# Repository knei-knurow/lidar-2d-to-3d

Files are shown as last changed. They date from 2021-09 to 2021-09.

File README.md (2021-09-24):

# Lidar 2D to 3D

Celem projektu było stworzenie urządzenia zdolnego do skanowania otaczającej go
przestrzeni w 3D z użyciem lidaru 2D.

ezgif-3-d5575b524c23

# Spis treści

- [Galeria](#galeria)
  - [3D](#3d)
  - [2D](#2d)
- [Submoduły](#submoduły)
  - [lidar-tools\*](#lidar-tools)
    - [sync\*](#sync)
    - [servoctl](#servoctl)
    - [receiver/transmitter](#transmitterreceiver)
    - [scan-dummy](#scan-dummy)
  - [lidar-avr\*](#lidar-avr)
  - [lidar-scan\*](#lidar-scan)
  - [lidar-vis](#lidar-vis)
  - [lidar-visualizations](#lidar-visualizations)
  - [lidar-stm32](#lidar-stm32)
- [Elementy](#elementy)
  - [Lidar](#lidar)
    - [Specyfikacja](#specyfikacja)
    - [Źródła](#źródła)
    - [Tryby skanowania](#tryby-skanowania)
    - [Dane](#dane)
    - [Pomiary szybkości silnika lidaru](#pomiary-szybkości-silnika-lidaru)
    - [Ogólne pomiary rezultatów lidaru](#ogólne-pomiary-rezultatów-lidaru)
  - [Serwomechanizm](#serwomechanizm)
  - [IMU](#imu)
    - [MPU-6050](#mpu-6050)
    - [MPU-9250](#mpu-9250)
    - [Kalibracja](#kalibracja)
    - [DMP](#dmp)
  - [Mikrokontroler](#mikrokontroler)
  - [Głowica](#głowica)
- [Skanowanie 3D](#skanowanie-3d)
  - [Obróbka surowych pomiarów IMU](#obróbka-surowych-danych-imu)
- [Konfiguracja](#konfiguracja)
  - [Hardware](#hardware)
  - [Software](#software)
    - [Parametry _lidar-tools/sync_](#parametry-lidar-toolssync)
- [Materiały](#materiały)
  - [Oprogramowanie pomocnicze](#oprogramowanie-pomocnicze)
  - [Przykłady chmur punktów](#przykłady-chmur-punktów)

# Galeria

## 3D

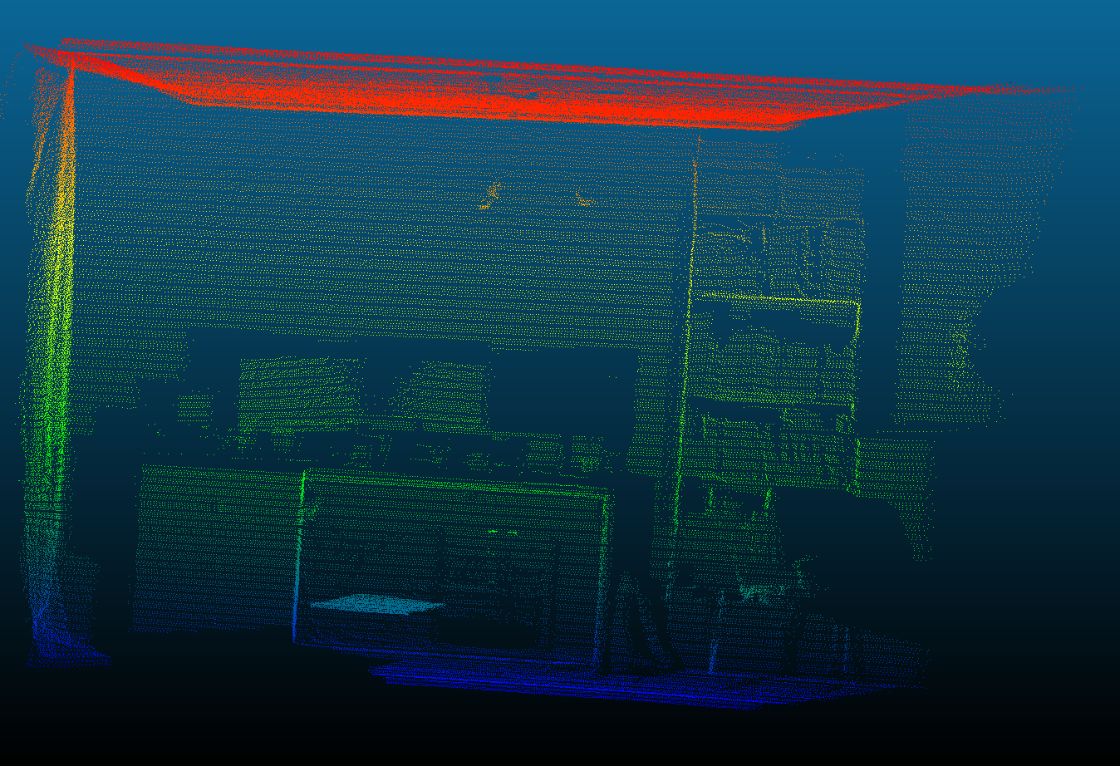
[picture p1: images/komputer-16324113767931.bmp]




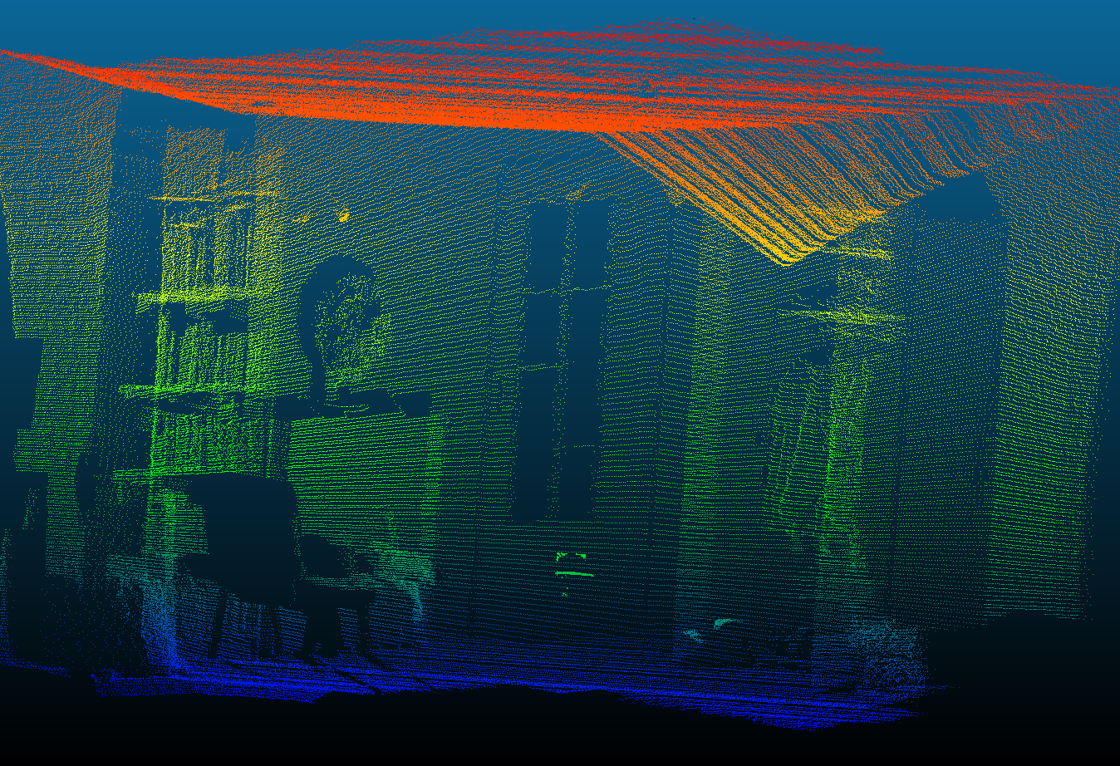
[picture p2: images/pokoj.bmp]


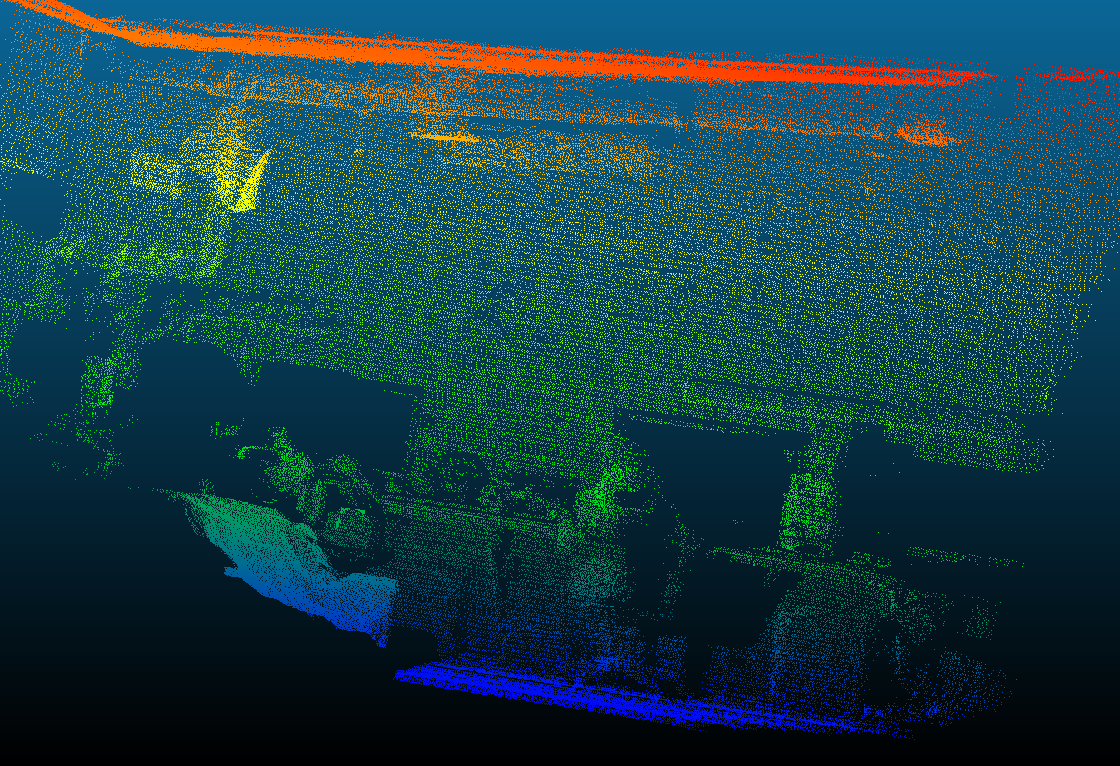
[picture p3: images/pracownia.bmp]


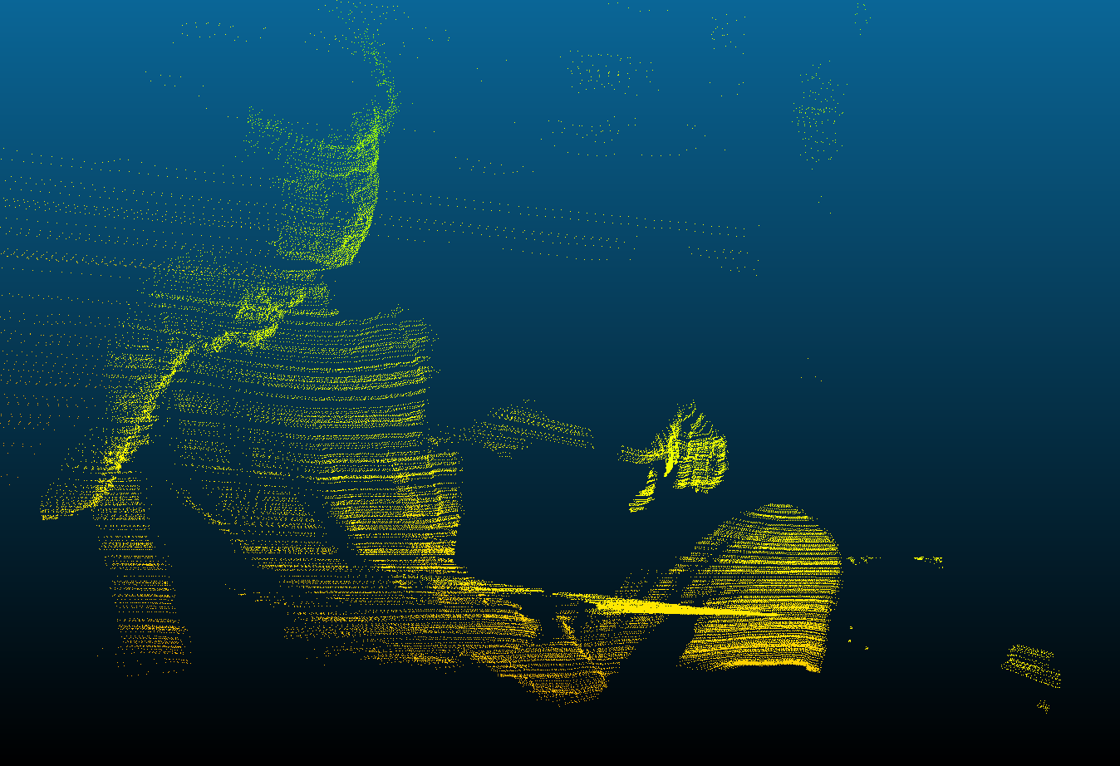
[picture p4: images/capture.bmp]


## 2D

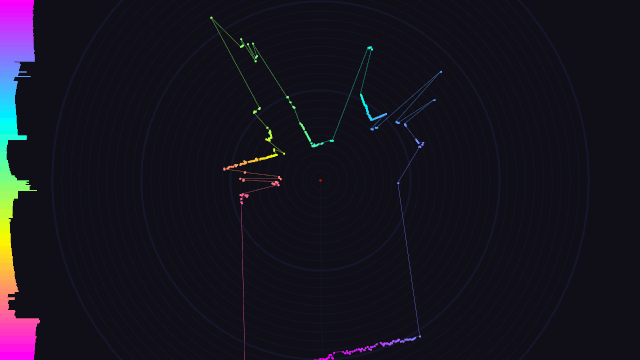
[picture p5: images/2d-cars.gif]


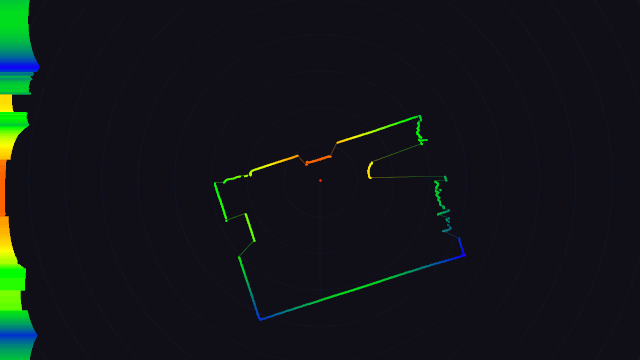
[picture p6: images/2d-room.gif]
2d-room


# Submoduły

W tym repozytorium pod jednym dachem zebrane są repozytoria z przedrostkiem
**lidar-** rozwijane w ramach [KNEI](https://github.com/knei-knurow), które
mają związek ze skanowaniem 3D. Więcej informacji o każdym
z tych projektów można znaleźć w ich plikach README.

**Gwiazdka \* oznacza repozytoria, które są wymagane do skanowania 3D.**
Pozostałe projekty mogą się przydać podczas zabawy ze skanowaniem 2D.

## lidar-tools\*

Zbiór programów _narzędzi_ przydatnych podczas pracy z lidarem.

### sync\*

Najważniejsze z _narzędzi_. Do jego zadań należy:

- Ustanowienie połączenia z mikrokontrolerem (który steruje serwem i
  akcelerometrem) oraz lidarem.
- Synchronizacja danych/pomiarów z dostępnych źródeł.
- Obliczanie punktów chmury 3D.
- Wypisywanie punkt po punkcie (x, y, z) na standardowe wyjście (stdout).

### servoctl

Wysyła do mikrokontrolera ramkę danych ustawiającą serwomechanizmu na zadanej pozycji.

### transmitter/receiver

Wysyła/odbiera dane lidaru 2D (uzyskane np. za pomocą _lidar-scan_) przez UDP.

### scan-dummy

Udaje _lidar-scan_. Generuje przykładowe dane.

**Autorzy:** [Szymon Bednorz](https://github.com/github.com/dsonyy),
[Bartek Pacia](https://github.com/github.com/bartekpacia)

## lidar-avr\*

Oprogramowanie przeznaczone do bycia wgranym na mikrokontroler AVR Atmega328p,
którego zadaniem jest obsługa serwomechanizmu i akcelerometru oraz komunikacja poprzez
USART z urządzeniem operatora.

Więcej o dokładnej konfiguracji i działaniu w dalszych sekcjach tego
dokumentu.

**Autorzy:** [Szymon Bednorz](https://github.com/github.com/dsonyy),
[Bartek Pacia](https://github.com/github.com/bartekpacia)

## lidar-scan\*

Projekt wywodzący się z _lidar-visualizations._ Pomysł polegał na stworzeniu
programu, który [robi jedną rzecz i robi ją dobrze](https://en.wikipedia.org/wiki/Unix_philosophy).

Zadaniem programu jest ustanowienie połączenia z lidarem oraz wypisywanie na
standardowe wyjście (stdout) odebranych danych w formie tekstowej. Docelowo
dane mogą być przekazane dowolnemu innemu programowi, który rozumie wejściowy
format danych.

Zgodny z systemami Linux, macOS, Windows.

**Przykładowe wyjście:**

```
# A comment
# ! ID Number   Elapsed time [ms]
# Angle [°]   Distance [mm]
! 0 0
120  100
240  100
360  100
! 1 500
120  200
240  200
360  200
! 2 500
```

**Autorzy:** [Szymon Bednorz](https://github.com/github.com/dsonyy),
[Bartek Pacia](https://github.com/github.com/bartekpacia)

## lidar-vis

Graficzie wyświetla dane otrzymane z lidaru za pomocą _lidar-scan_.

Projekt wywodzący się z _lidar-visualizations_. Jest to "siostrzany" program do
\_lidar-scan – [robi jedną rzecz i robi ją dobrze](https://en.wikipedia.org/wiki/Unix_philosophy).

Zgodny z systemami Linux, macOS, Windows.

**Autorzy:** [Szymon Bednorz](https://github.com/github.com/dsonyy),
[Bartek Pacia](https://github.com/bartekpacia)

## lidar-visualizations

Wyświetla dane z lidaru w postaci tekstowej lub graficznej w czasie rzeczywistym.

Oprogramowanie kilkukrotnie zmieniło prawie całkowicie swoją formę. Stworzone
zostało na potrzeby artykułu do "Elektroniki Praktycznej". Na chwilę obecną
nie jest aktywnie rozwijane. Kod składa się z kilku interfejsów, które
teoretycznie umożliwiają tworzenie dodatkowych funkcjonalności. Program
korzysta z oficjalnego RPLIDAR SDK oraz wysokopoziomowej biblioteki
graficznej SFML.

Zgodny z systemami Linux, macOS, Windows.

Więcej informacji można przeczytać w artykule ["Wizualizacja pomiarów skanera LIDAR"](https://ep.com.pl/kursy/notatnik-konstruktora/14763-wizualizacja-pomiarow-skanera-lidar) w ["Elektronice Praktycznej"](https://ep.com.pl) z marca 2021.

**Autor:** [Szymon Bednorz](https://github.com/github.com/dsonyy)

## lidar-stm32

Ciekawy projekt, który podobnie jak _lidar-visualizations_, stworzony został na
potrzeby "Elektroniki Praktycznej". Uruchamiany jest na płytce STM32, która za
pomocą UART wysyła/odbiera dane do/z lidaru, a następnie je wizualizuje.

RPLIDAR SDK nie jest przystosowany do urządzeń _embeddeed_, więc na jego
podstawie stworzona została autorska implementacja przeznaczona na STM32.

Więcej informacji można przeczytać w artykule ["Wizualizacja pomiarów skanera LIDAR"](https://ep.com.pl/kursy/notatnik-konstruktora/14763-wizualizacja-pomiarow-skanera-lidar) w ["Elektronice Praktycznej"](https://ep.com.pl) z marca 2021.

**Autor:** [Bartek Dudek](https://github.com/github.com/doodek)

# Elementy

## Lidar

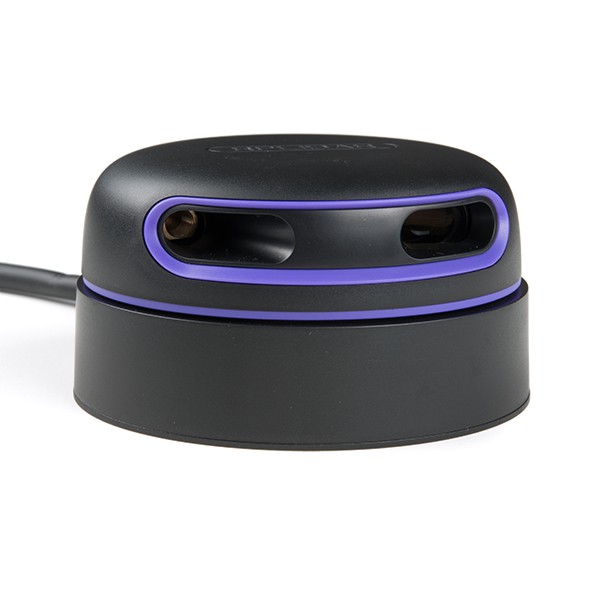
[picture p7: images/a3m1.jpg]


Wykorzystywany w projekcie lidar to [Slamtec RPLIDAR A3](https://www.slamtec.com/en/Lidar/A3Spec).
Producent dostarcza także [RPLIDAR SDK](https://github.com/Slamtec/rplidar_sdk)
wspierające systemy Linux, macOS i Windows, które pozwala na pracę ze sprzętem.

Lidar posiada swoje własne zasilanie. Dysponuje również przewodem USB, aby
przesyłać dane do urządzenia operatora.

### Specyfikacja

| Wielkość | A3 |
| --- | --- |
| Zakres pomiarów | do 25m |
| Częstotliwość pomiarów | do 16kHz |
| Częstotliwość wykonywania chmur | 5Hz - 20Hz |
| Rozdzielczość kątowa | do 0.225°  |
| Interfejs komunikacji | TTL UART |
| Prędkość komunikacji | 256000bps  |

### Źródła

- [RPLIDAR A3](https://www.slamtec.com/en/Lidar/A3)
- [SDK GitHub](https://github.com/Slamtec/rplidar_sdk)
- [RPLIDAR A3 User Manual](https://download.kamami.pl/p573426-LM310_SLAMTEC_rplidarkit_usermanual_A3M1_v1.0_en.pdf)
- [RPLIDAR A3 Introduction and Datasheet](https://download.kamami.pl/p573426-LD310_SLAMTEC_rplidar_datasheet_A3M1_v1.3_en.pdf)

### Tryby skanowania

RPLIDAR oferuje kilka trybów skanowania. Godne uwagi są tylko dwa: domyślny
sensitivity (indoor) i stability (outdoor). Podczas pracy na zewnątrz,
szczególnie w bardzo słoneczne dni, wyraźnie widać różnicę w ilości poprawnie
wykonanych pomiarów. Pozostałe tryby istnieją dla kompatybilności wstecznej z poprzednimi generacjami urządzenia i/lub wymagają niższego baudrate'u podczas transmisji danych.

| ID  | Scan mode | Sample time [us] | Frequency |
| --- | --- | --- | --- |
| 0 | Standard | 252 | 0.484406  |
| 1 | Express | 126 | 0.968812  |
| 2 | Boost | 63 | 1.93762 |
| 3 | **Sensitivity/Indoor (domyślny)** | 63 | 1.93762 |
| 4 | **Stability/Outdoor** | 100 | 1.2207 |

### Dane

- Domyślnym formatem danych lidaru są pary (kąt, odległość) w jednostkach
  [stopnie, milimetry].
- Pary pomiarów są pogrupowane po 360 stopni - jedna chmura punktów.
- Jeżeli pomiar dla danego kąta się nie powiódł, wartość odległości jest równa 0.
- Maksymalna ilość punktów w jednej chmurze to 8192, jest to narzucone przez
  producenta ograniczenie.
- Ilość punktów w chmurze - 360 stopniach - zależy od trybu skanowania oraz od
  ilości obrotów na minutę (ang. RPM, revolutions per minute). Im wolniejsza prędkość obrotu, tym więcej punktów w chmurze. Zalecany przez autora zakres pracy to od 200 do 1023 rpm. Przy mniejszych wartościach niż 200 istnieje ryzyko przekroczenia wartości 8192 punktów na chmurę co może powodować problemy. Domyśla wartość to 660rpm.

### Pomiary szybkości silnika lidaru

| Software RPM | Measured RPM | Software RPS | Measured RPS | Error  |
| --- | --- | --- | --- | --- |
| 200 | 196.62 | 3.33 | 3.28 | ~1.7%  |
| 400 | 432.02 | 6.67 | 7.20 | ~8.0%  |
| 600 | 684.52 | 10.00 | 11.41 | ~14.0% |
| 800 | 965.14 | 13.33 | 16.09 | ~20.6% |
| 1000 | 1268.98 | 16.67 | 21.15 | ~26.8% |

### Ogólne pomiary rezultatów lidaru

Tryb skanowania: **Sensitivity**

| zadany RPM | całk. czas [s] | punktów | punktów na chmurę | chmur | śr. czas na chmurę [s] | zmierzony RPM |
| --- | --- | --- | --- | ----- | --- | --- |
| 200 | 28.369 | 447133  | 4860.14 | 92 | 0.31 | 194.58 |
| 400 | 28.187 | 444097  | 2198.50 | 202 | 0.14 | 429.99 |
| 600 | 28.308 | 446794  | 1387.56 | 322 | 0.09 | 682.49 |
| **660\***  | 28.378 | 448529  | 1274.23 | 352 | 0.08 | 744.24 |
| 800 | 26.792 | 423121  | 984.00 | 430 | 0.06 | 962.97 |
| 1000 | 27.327 | 432130  | 748.93 | 577 | 0.05 | 1266.88 |

\* domyślny

## Serwomechanizm

Serwomechanizm odpowiada za obrót płaszczyzny, która jest skanowana przez lidar.
Sterowane jest ono sygnałem PWM za pomocą mikrokontrolera.

Wymaga własnego zasilania.

## IMU

IMU (ang. inertial measurement unit) to urządzenie służące do nawigacji
inercyjnej wyposażone w akcelerometr i żyroskop. Układ wykorzystywany przez nas
to **MPU-6050** o 6 stopniach swobody (akcelerometr X, Y, Z i żyroskop X, Y, Z).
W początkowej fazie rozwoju projektu zauważono, że konstrukcja składająca się z
samego lidaru i serwa może być podatna na niedokładności spowodowane tym, że:

- konstrukcja podczas ruchu mogłaby być mniej lub bardziej przechylana w każdą
  ze stron podczas skanowania,
- wykorzystywany przez nas serwomechanizm ma ograniczoną dokładność.

Oba problemy miały zostać rozwiązane przez IMU, które dostarczałoby w czasie
rzeczywistym danych dotyczących aktualnego przechylenia/obrotu płaszczyzny
skanowania.

Niestety wyniki z wykorzystujące opisane IMU i metody szacowania obrotu
płaszczyzny okazują się jeszcze bardziej niedokładne, niż wykorzystywanie
samego lidaru i serwa. Powodów należy szukać w szacowaniu pozycji, które polega
na ciągłym aktualizowaniu stanu, opierającego się na poprzednich pomiarach. W
ten sposób bardzo szybko rośnie błąd, który sprawia, że dwa skany tej samej
sceny mogą mocno różnić się od siebie.

Projekt w wersji finalnej przygotowany jest do pracy **z** jak i **bez** IMU.
Dla lepszych rezultatów zalecane jest niekorzystanie z IMU. Jeżeli zamierza
się ruszać konstrukcją podczas skanowania, można zdecydować się jego
wykorzystanie, chociaż ma się wtedy do czynienia z rosnącym błędem.

### MPU-6050

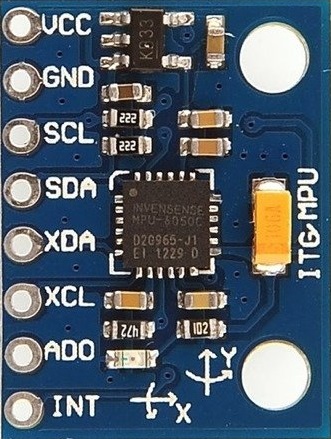
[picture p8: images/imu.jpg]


Podstawową funkcjonalnością urządzenia jest wykorzystywanie 3-osiowego
akcelerometru i żyroskopu. W ten sposób otrzymujemy strumień _surowych_
pomiarów składających się z sześciu 2-bajtowych liczb zmiennoprzecinkowych
w opisanej w dokumentacji skali. Moduł komunikuje się interfejsem I2C.

[MPU-6050 w bazie i2cdevlib](https://www.i2cdevlib.com/devices/mpu6050#links)

### MPU-9250

Moduł całkowicie kompatybilny z MPU-6050. Różnicą jest posiadanie dodatkowo
3-osiowego magnetometru, który wymaga specjalnej kalibracji. Magnetometr
aktualnie nie jest wykorzystywany w projekcie.

### Kalibracja

Kalibracja MPU-6050 polega na ustawieniu go na możliwie płaskiej powierzchni,
wykonanie serii pomiarów (po 6 wartości na pomiar), obliczenie ich średniej i
zapisanie wyników. Należy też uwzględnić przyspieszenie grawitacyjne, które
powinno być wyraźnie widoczne na jednej z osi. Wyniki kalibracji powinny zostać
z odpowiednim znakiem dodane do każdego późniejszego pomiaru.

Program _lidar-tools/sync_ wykonuje kalibrację automatycznie przed rozpoczęciem
skanowania (jeżeli korzystamy z IMU).

### DMP

Ciekawą częścią MPU jest moduł DMP (Digital Motion Processor), którym chwali
się producent, ale jednocześnie oficjalne dokumentacje całkowicie pomijają jego
istnienie. W internecie znaleźć można liczne nieoficjalne dyskusje i biblioteki
próbujące wykorzystywać jego funkcjonalności. Do jednej z wielu (w tym dalej
nieodkrytych) funkcjonalności należy szacowanie obrotu na podstawie _surowych_
danych (obliczanie kwaternionu).

## Mikrokontroler

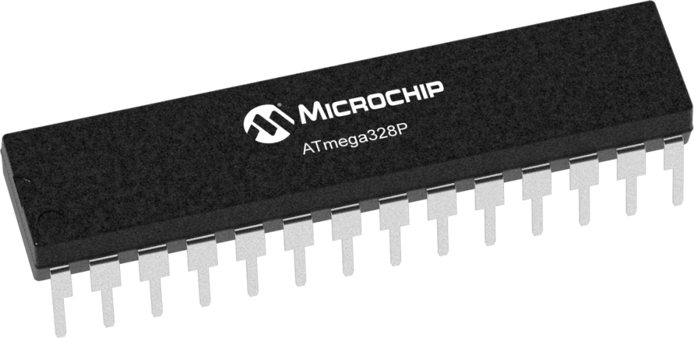
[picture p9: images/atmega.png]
 

Wykorzystywany w projekcie mikrokontroler to ATmega328p. Oprogramowanie, które
musi się na nim znaleźć znajduje się w repozytorium _lidar-avr_. Odpowiada ono
za:

- sterowanie sygnałem PWM w celu kontroli serwomechanizmu,
- komunikacja poprzez I2C z MPU-6050 (lub MPU-9250),
- komunikacja z komputerem operatora (odbieranie/wysyłanie ramek danych).

Szczegóły na temat połączeń przewodów i elementów projektu znajduje się w sekcji [hardware](#hardware) (wykorzystana została płytka Arduino UNO, ale mikrokontroler jest
programowany bezpośrednio).

## Głowica

Mechaniczna konstrukcja na której zamontowane są poszczególne elementy projektu.

### Prototyp

ezgif-3-d5575b524c23

### Wersja finalna

Konstrukcja zaprojektowana w programie Autodesk Fusion 360 i wydrukowana w
technologii 3D.

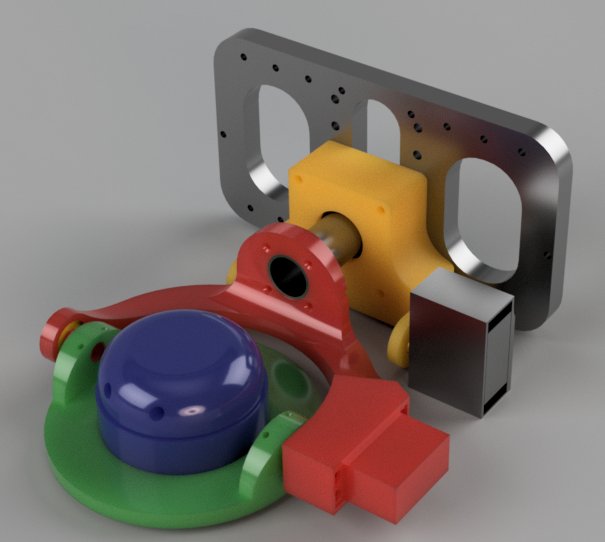
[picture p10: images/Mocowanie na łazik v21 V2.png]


# Skanowanie 3D

Skanowania 3D polega na zbieraniu danych z kilku źródeł i łączeniu ich
w taki sposób, aby otrzymać informację o otoczeniu.

Najważniejszym urządzeniem jest lidar, który po uruchomieniu jest w stanie
generować kilka chmur punktów na sekundę. Punkty reprezentowane są w postaci
par (kąt, odległość) w jednostkach [stopnie, milimetry].

Kolejnym istotnym elementem jest serwomechanizm. Znana jest zadana przez nas
pozycja na jaką ma się ustawić. W tym celu wykorzystywana jest wewnętrzna
jednostka, która może zostać przeliczona na stopnie.

Ostatnim (ale opcjonalnym) elementem jest IMU, który dostarczać może pomiary w
postaci 3 wartości (x, y, z) akcelerometru, 3 wartości (x, y, z) żyroskopu.

Program **lidar-tools/sync** po uruchomieniu na urządzeniu operatora:

1. tworzy subproces i uruchamia program **lidar-scan**, który łączy się z
   podłączonym do urządzenia operatora lidarem; uruchamia pętlę odbierająca od
   lidar-scan pomiary **lidaru**,
2. łączy się z mikrokontrolerem, na którym powinien znajdować się program
   **lidar-avr**.
3. uruchamia pętlę wysyłającą rozkazy do mikrokontrolera sterującą
   **serwomechanizmem**.
4. uruchamia (opcjonalnie) pętlę odbierająca od mikrokontrolera pomiary **IMU**.

Pomiary IMU i zadane pozycje serwomechanizmu są gromadzone wraz z czasem, w
którym miały miejsce. Do każdej odebranej chmury punktów lidaru dobierany jest
najlepiej pasujący czasowo pomiar IMU lub zadana pozycja serwomechanizmu.
Metoda jaka zostanie obrana zależy od użytkownika (innymi słowy, to użytkownik
decyduje, czy wykorzystywać IMU czy zadane pozycje serwomechanizmu).

Następnie dokonywane są obliczenia, w efekcie których powstaje grupa gotowych
punktów. Wypisywane są one na standardowe wyjście (stdout).

### Obróbka surowych pomiarów IMU

MPU-6050 dostarcza sześć 2-bajtowych zmiennoprzecinkowych wartości w każdym
_surowym_ pomiarze. Aby zrozumieć dane, można je łatwo zwizualizować na wykresie.
Będą one odpowiadały ruchom i obrotom urządzenia.

[Film z wizualizacją](https://youtu.be/J4pH3LHojVM)

**Przykładowy wykres:**



_Surowe_ dane po odebraniu przez _lidar-tools/sync_ są przekazywane estymatora
pozycji (ang. attitude estimator), który aktualizowany jest o kolejne wartości.
Jako wynik estymator zwraca [kwaternion](https://pl.wikipedia.org/wiki/Kwaterniony) - obiekt matematyczny składającą się z 4 liczb zmiennoprzecinkowych (w, x, y, z),
które mogą zostać zinterpretowane jako obrót obiektu.

# Konfiguracja

## Hardware

1. Mikrokontroler musi być podłączony do urządzenia operatora, aby umożliwić
   komunikację USART.
2. Serwomechanim musi być połączony do zasilania oraz mikrokontrolera w sposób
   przedstawiony na schemacie.
3. IMU (MPU-6050 lub kompatybilne MPU-9250) może być podłączone do mikrokontrolera
   w sposób przedstawiony na schemacie.
4. Lidar musi być podłączony do stabilnego źródła zasilania i do urządzenia
   operatora.

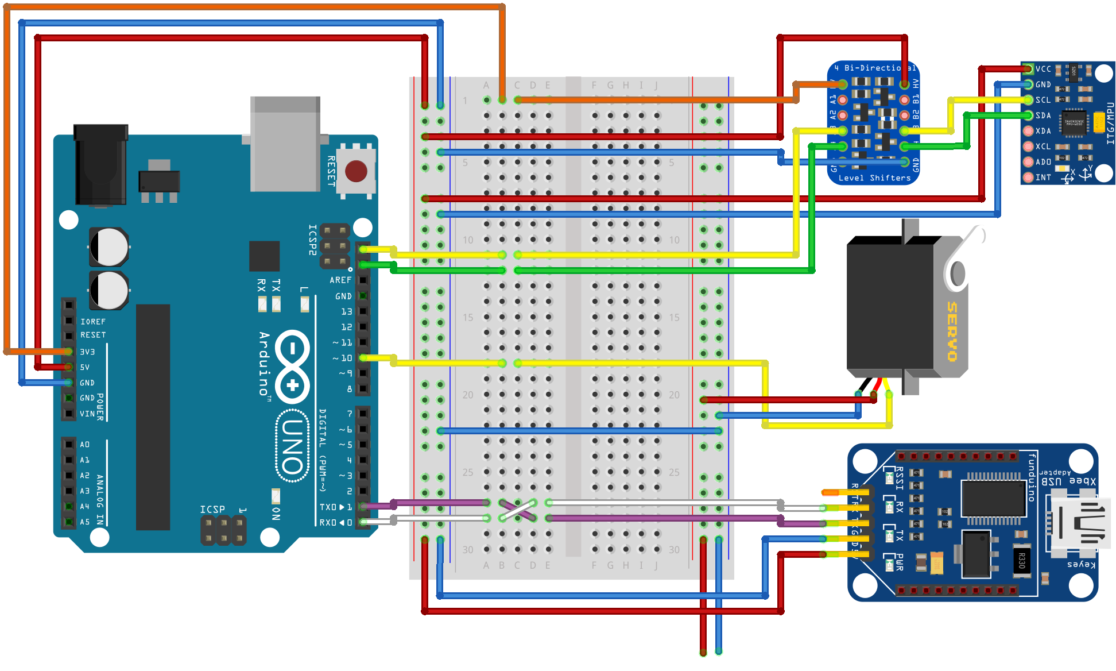
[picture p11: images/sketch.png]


## Software

**Na mikrokontrolerze** musi być zaflashowany program _lidar-avr_.

**Na urządzeniu operatora** musi znaleźć się:

- _lidar-tools/sync_
- _lidar-scan_

Następnie można przystąpić do konfiguracji _lidar-tools/sync_. Wszystkie dostępne
parametry programu należy dostrajać korzystając z argumentów wiersza poleceń.
Ich liczba może być spora, dlatego wygodnie jest przygotować skrypt, który
uruchomi _lidar-tools/sync_ przekazując mu odpowiednie parametry (jak np.
_sync.ps1_ znajdujący się w głównym repozytorium projektu _lidar-tools_).

### Parametry _lidar-tools/sync_

| Parametr | Opis | Uwagi |
| --- | --- | --- |
| avrport | port, przez który odbywa się komunikacja z mikrokontrolerem | |
| avrbaud | baudrate, z którego korzysta mikrokontroler do komunikacji | domyślnie 19200 |
| lidarexe | ścieżka do pliku wykonywalnego _lidar-sync_ | |
| lidarport | port, przez który odbywa się komunikacja z lidarem | |
| lidarmode | tryb pracy lidaru | 3 (indoor, domyślnie) lub 4 (outdoor) |
| lidarpm | ilość obrotów na minutę lidaru (RPM) | 200-1023, domyślnie 660 |
| servostep | pojedynczy krok serwomechanizmu w jego jednostkach | |
| servodelay | odstęp czasowy serwomechanizmu pomiędzy krokami w milisekundach | |
| servomin | minimalna pozycja serwomechanizmu w jego jednostkach | domyślnie 1000 |
| servomax | maksymalna pozycja serwomechanizmu w jego jednostkach | domyślnie 3000 |
| servocalib | pozycja serwomechanizmu, dla której płaszczyzna lidaru będzie w możliwie równoległej do ziemi pozycji | domyślnie 2500 |
| servostart | pozycja startowa serwomechanizmu do skanowania | domyślnie 3000 |
| servounit | ważna wartość wyznaczona eksperymentalnie, która służy do przeliczenia jednostki serwomechanizmu na stopnie: **1 jednostka serwa = _servounit_ °** | domyślnie około -0.047 |
| cloudrotation | wszystkie punkty leżące na płaszczyźnie zeskanowanej przez lidar zostaną obrócone o _cloudrotation_ radianów | dla głowicy prototyp: -π/4, (-0.785398) |
| acceluse | jeżeli prawda to bierze pod uwagę IMU, jeśli fałsz to tylko zadane pozycje serwomechanizmu | _true_ lub _false_ |

# Materiały

## Oprogramowanie pomocnicze

Oprogramowanie, które powstało jako pomoc podczas pracy nad projektami. Są to
proste programy/skrypty realizujące jedno zadanie.

- [serial-read-accelerometer](https://github.com/dsonyy/go-stuff)
- [accel-plot](https://github.com/dsonyy/python-stuff)
- [angle-visualization](https://github.com/dsonyy/cpp-stuff)
- [pipeline](https://github.com/dsonyy/go-stuff)
- [attestimator](https://github.com/knei-knurow/attestimator)

## Przykłady chmur punktów

- [3D (Google Drive)](https://drive.google.com/drive/folders/1JSF53_TLBTgeE407KCZTTn-GNv1g_iZ-?usp=sharing)
- [2D (Google Drive)](https://drive.google.com/drive/folders/1GGNDYH1F7mPqHnHaxzhhpN3W45uAHUO9?usp=sharing)

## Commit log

2021-09-05 add lidar-xxx submodules
2021-09-25 sketch file
    [sketch.fzz]
